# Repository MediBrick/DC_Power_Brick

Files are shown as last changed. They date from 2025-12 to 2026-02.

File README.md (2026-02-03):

# Power Brick

The Power Brick can control power to resistive heater, thermo electric cooler/heater or DC motor.
It requires 8V or larger input and might be able to handle 30A (4 oz copper).

## Two Channel DC Power Controller.
  - DRV8704 FET driver
  -  8..52V
  -  SPI interface for  monitoring
  -  PWM 500kHz
  -  CSD18540Q5B FET 30 / 400A (peak)

[Datasheet Driver](./datasheets/drv8704.pdf)
[Datasheet FET](./datasheets/csd18540q5b.pdf)

### Overview
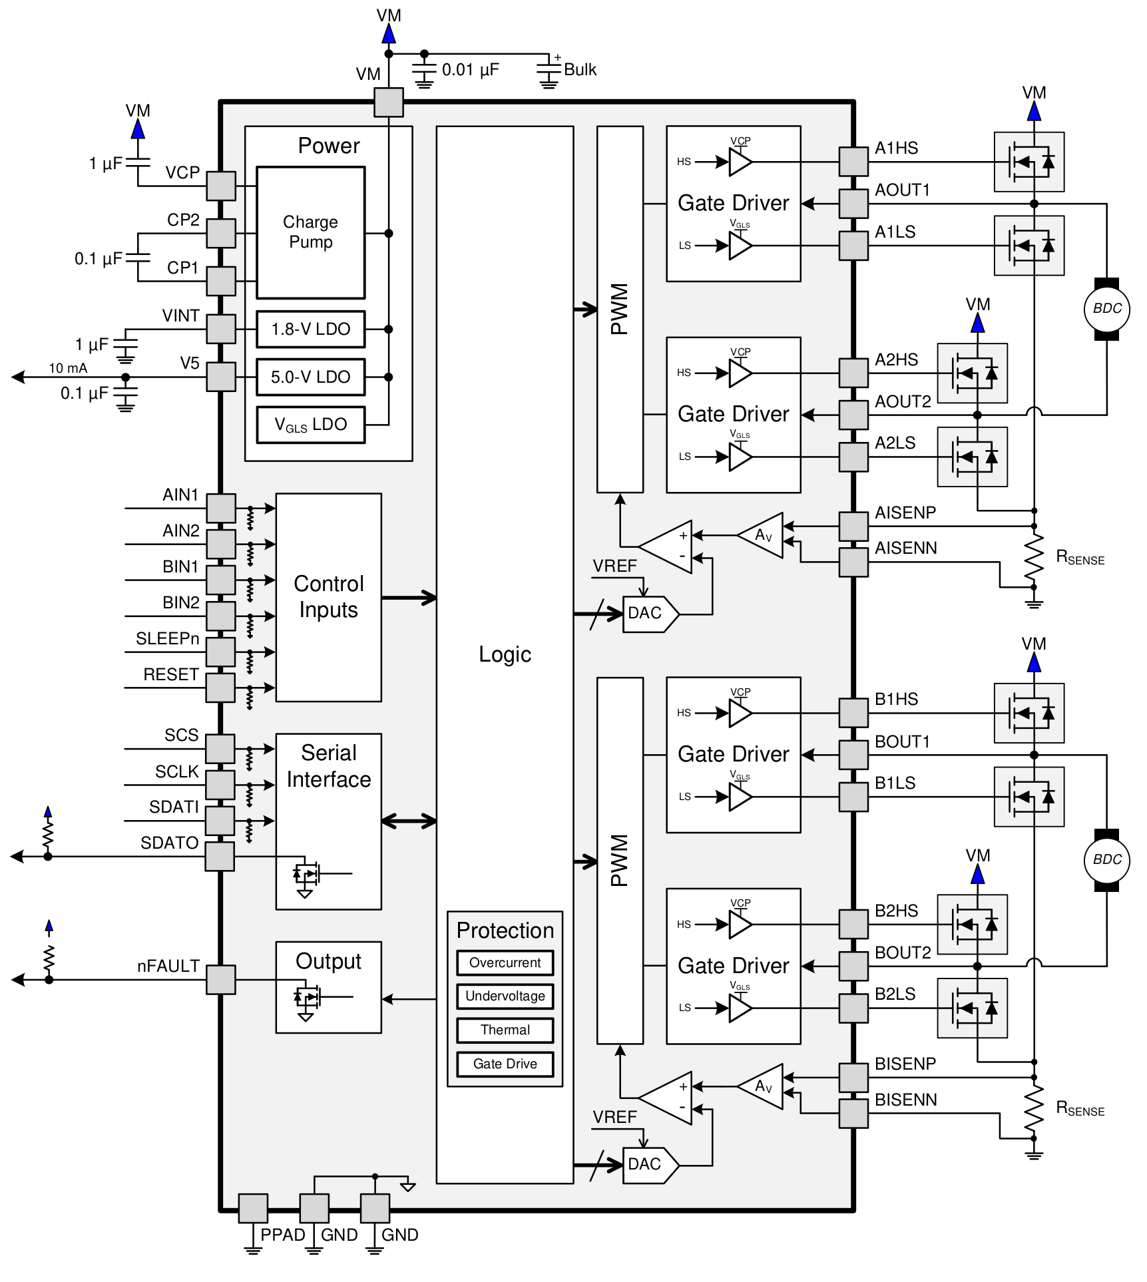
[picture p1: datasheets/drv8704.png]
DRV8704


### Control Logic
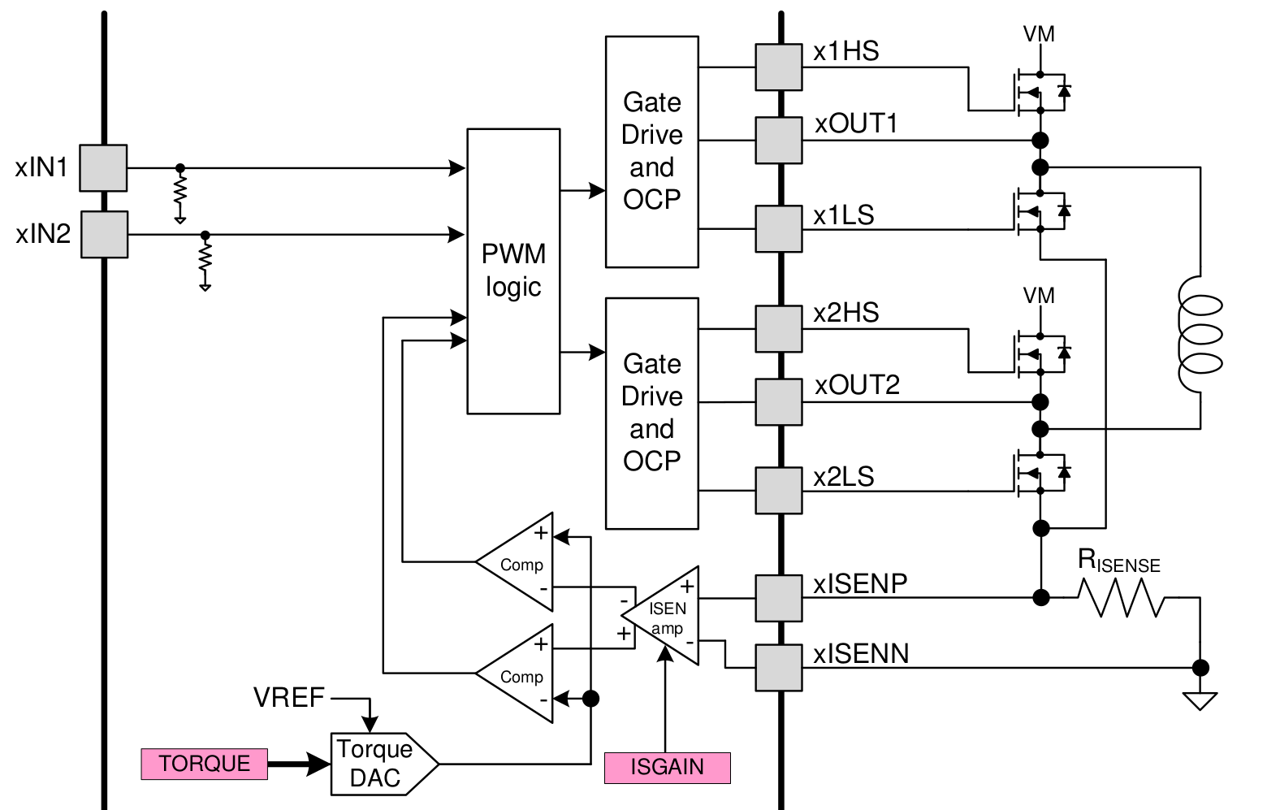
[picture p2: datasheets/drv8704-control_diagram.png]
DRV8704-diagram

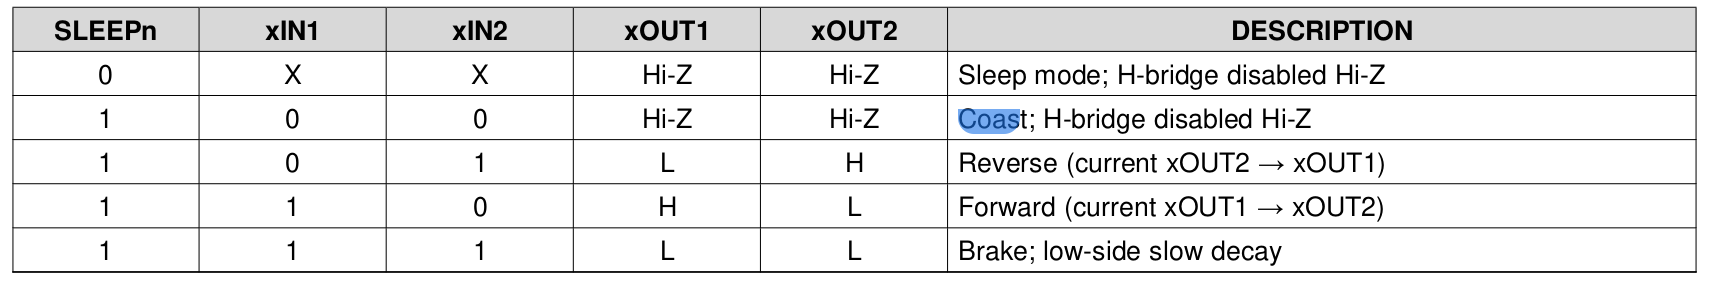
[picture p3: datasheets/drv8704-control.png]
DRV8704-control


## 2x Two Channel Precision Thermistor ADC
  - ADS1220
  - Configured for two channel 10K NTC thermistor measurements using internal current source and external reference 22k resistor.

[Datasheet ADS1220](./datasheets/ads1220.pdf)

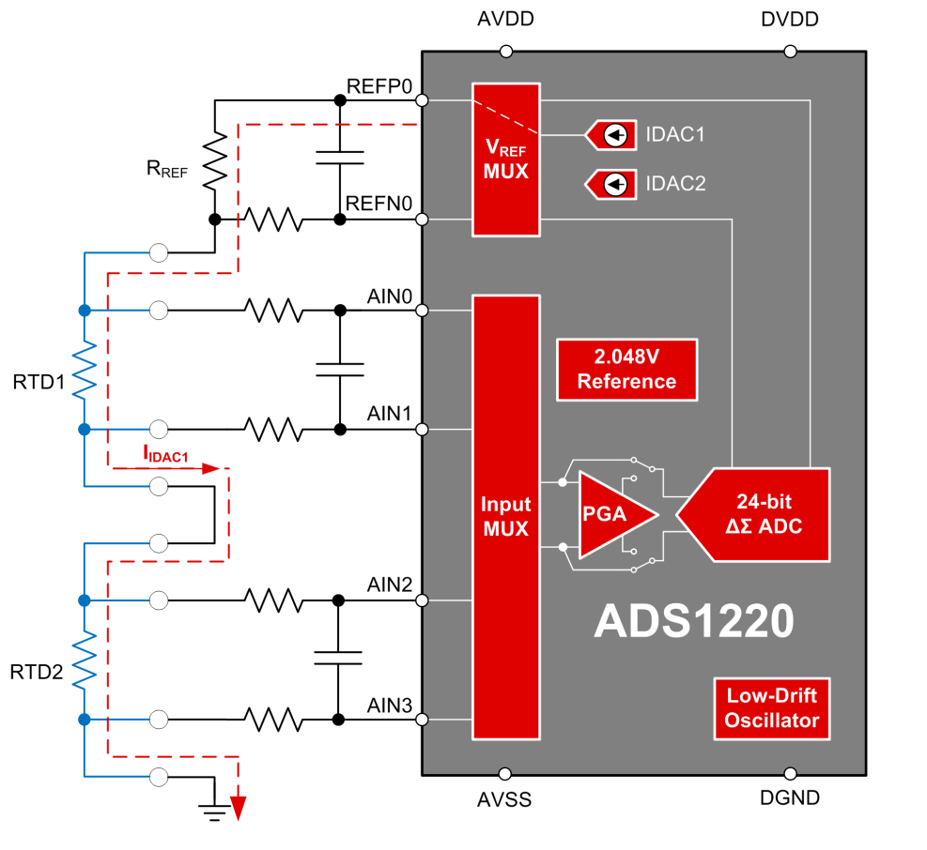
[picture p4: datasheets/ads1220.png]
ADS1220


This design requires that both temperature sensors are attached. If one is not populated, the measurement circuit is interrupted and no temperature is reported.

## Power Brick PCB Design

The following files were created for this project using KiCad.

Schematics

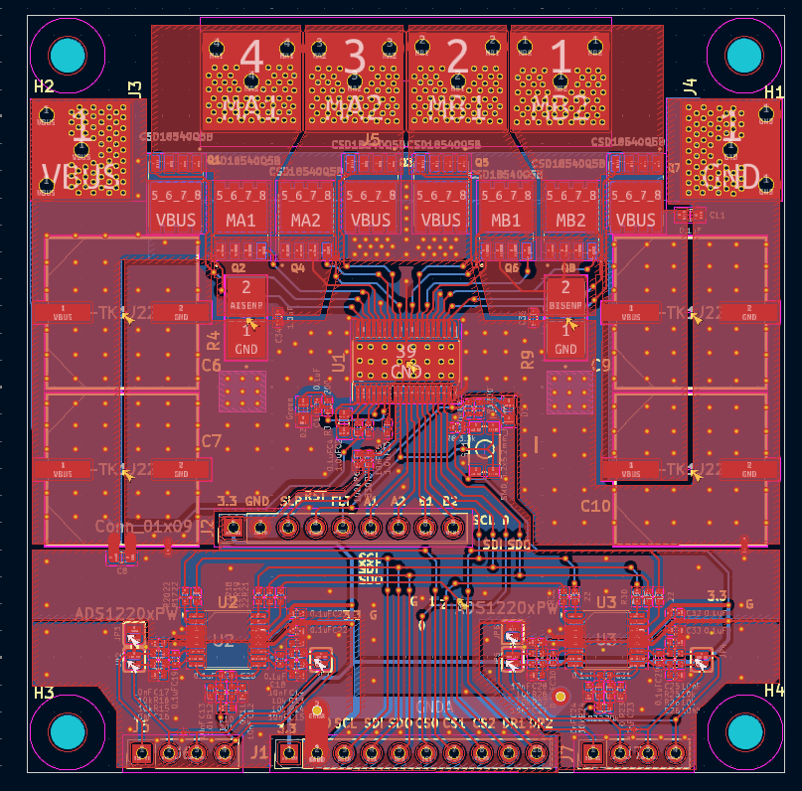
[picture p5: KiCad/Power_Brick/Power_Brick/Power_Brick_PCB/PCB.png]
Schematics

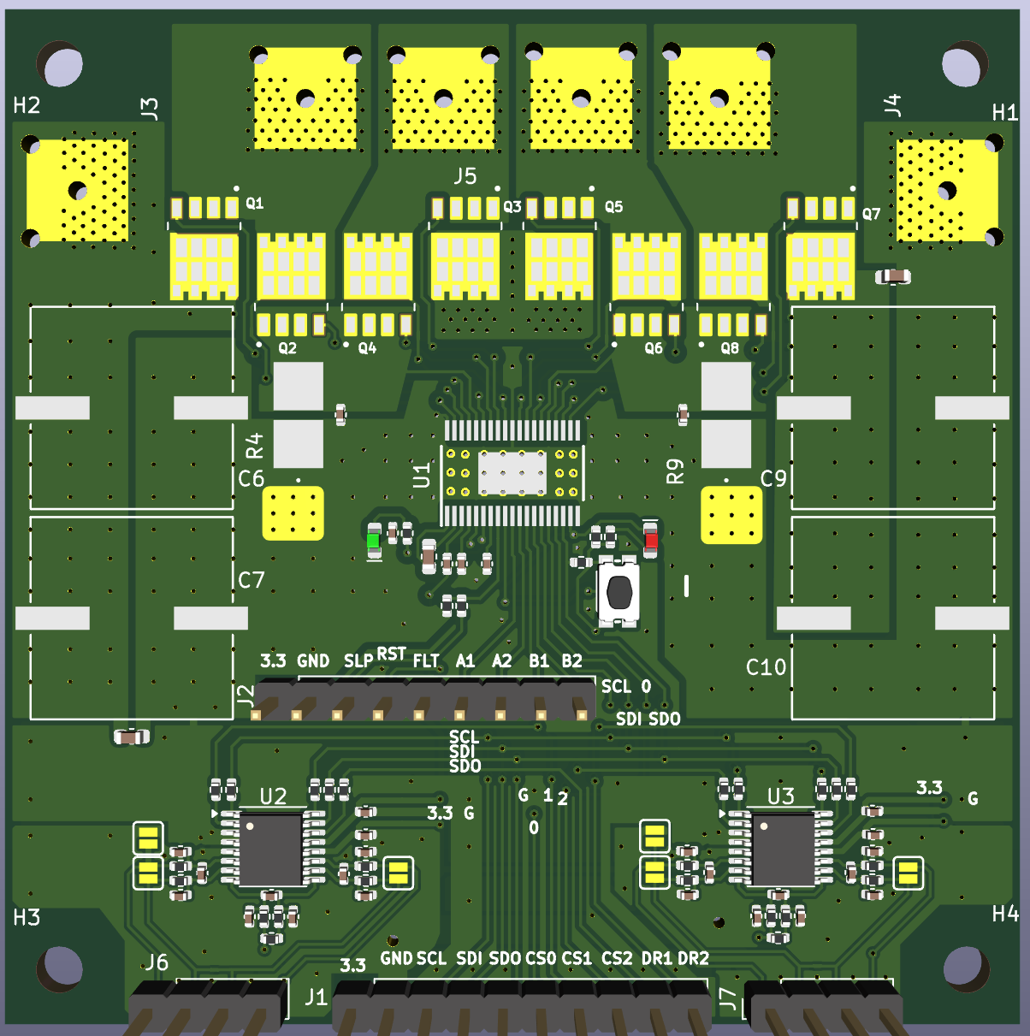
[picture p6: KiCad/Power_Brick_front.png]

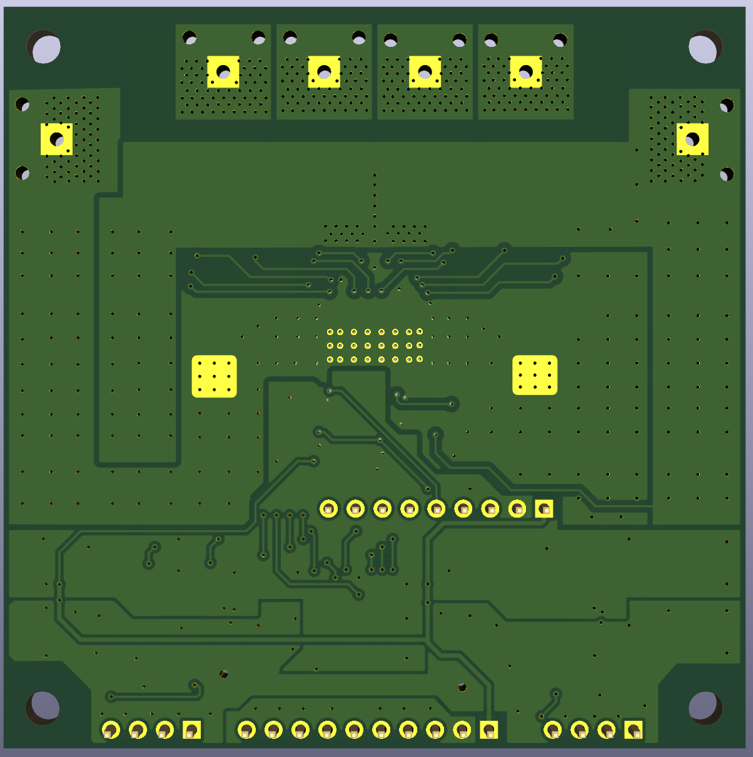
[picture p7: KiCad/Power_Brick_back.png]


[Bill of Materials](./DC%20Power%20Brick%20BOM.xlsx)
[Gerber Files](./)

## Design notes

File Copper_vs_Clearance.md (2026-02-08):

| Copper Weight (oz/ft²) | Thickness (µm) | Thickness (mm) | Standard Min Trace / Space (mm) | Advanced Min Trace / Space (mm) | Typical Use |
| --- | --- | --- | --- | --- | --- |
| 0.5 oz | ~18 µm | 0.018 mm | 0.10 / 0.10 | 0.075 / 0.075 | Fine-pitch logic |
| 1 oz | ~35 µm | 0.035 mm | 0.15 / 0.15 | 0.10 / 0.10 | General purpose  |
| 2 oz | ~70 µm | 0.070 mm | 0.20 / 0.20 | 0.15 / 0.15 | Moderate power |
| 3 oz | ~105 µm | 0.105 mm | 0.25 / 0.25 | 0.20 / 0.20 | Power drivers |
| 4 oz | ~140 µm | 0.140 mm | 0.30 / 0.30 | 0.25 / 0.25 | High current |
| 6 oz | ~210 µm | 0.210 mm | 0.40 / 0.40 | 0.30 / 0.30 | Power supplies |
| 8 oz | ~280 µm | 0.280 mm | 0.50 / 0.50 | 0.40 / 0.40 | Motor control |
| 10 oz | ~350 µm | 0.350 mm | 0.60 / 0.60 | 0.50 / 0.50 | Industrial power |
| 12 oz | ~420 µm | 0.420 mm | 0.75 / 0.75 | 0.60 / 0.60 | Extreme current  |

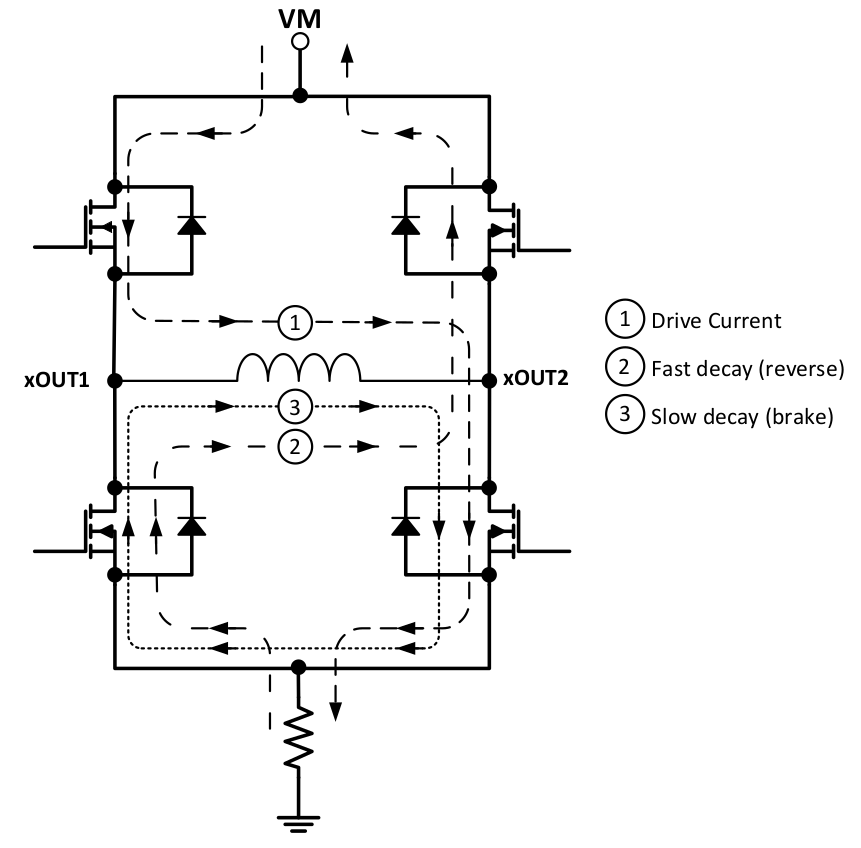
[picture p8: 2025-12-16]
datasheets/H-Bridge.png

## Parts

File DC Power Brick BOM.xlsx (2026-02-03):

Item # | Designator | Qty | Manufacturer | Mfg Part # | LCSC Part# | U.S. Distributor | Description / Value | Packaging | Type | Cost | Footprint | Remark
1 | C17,C26,C15,C5,C13,C24,C16,C12,C14,C28,C27,C23,C25 | 13 | Samsung Electro-Mechanics (https://www.lcsc.com/brand-detail/254.html) | CL05B103KC5VPNC | C16193410 (https://www.lcsc.com/product-detail/C16193410.html) |  | 10nF X7R ±10% 100V 0402 Ceramic Capacitors RoHS | 402 | SMD |  | C_0402_1005Metric
2 | Q2,Q8,Q6,Q5,Q4,Q3,Q7,Q1 | 8 | TI | CSD18540Q5B | C86513 (https://www.lcsc.com/product-detail/C86513.html?s_z=n_CSD18540Q5B) |  | CSD18540Q5B MOSFET N CH 60V |  | SMD | 1.5 | TRANS_CSD18540Q5B
3 | R25,R14,R28,R13,R2,R16,R26,R12,R24,R15,R27 | 11 | YAGEO (https://www.lcsc.com/brand-detail/396.html) | RC0402FR-0710KL | C60490 (https://www.lcsc.com/product-detail/C60490.html?s_z=n_402%252010K) |  | RES 10kΩ ±1% 62.5mW 0402 | 402 | SMD |  | R_0402_1005Metric
4 | C10,C7,C6,C9 | 4 | PANASONIC (https://www.lcsc.com/brand-detail/121.html) | EEETK1J221AQ | C401915 (https://www.lcsc.com/product-detail/C401915.html?s_z=n_EEE-TK1J221AQ) | Digikey Link incase LCSC is outofstock (https://www.digikey.com/en/products/detail/panasonic-electronic-components/EEE-TK1J221AQ/1975563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) | CAP ALUM 220uF ±20% 63V SMD |  | SMD | 3 | CAP_PAN_EEE_H13_PAN
5 | R32,R19,R29,R21,R31,R33,R30,R20,R18,R17 | 10 | YAGEO (https://www.lcsc.com/brand-detail/396.html) | RC0402FR-0722RL | C114765 (https://www.lcsc.com/product-detail/C114765.html?s_z=n_402%252022) |  | RES 22Ω ±1% 62.5mW 0402 | 402 | SMD |  | R_0402_1005Metric
6 | R10,R22 | 2 | YAGEO (https://www.lcsc.com/brand-detail/396.html) | RC0402FR-0720KL | C93942 (https://www.lcsc.com/product-detail/C93942.html?s_z=n_402%252020k) |  | RES 20kΩ ±1% 62.5mW 0402 | 402 | SMD |  | R_0402_1005Metric
7 | C4,C8,C11 | 3 | Samsung Electro-Mechanics (https://www.lcsc.com/brand-detail/254.html) | CL10B104KC8NNNC | C15725 (https://www.lcsc.com/product-detail/C15725.html) |  | CAP CER 100nF 100V X7R 0603 | 603 | SMD |  | C_0603_1608Metric
8 | C34,C35 | 2 | Samsung Electro-Mechanics (https://www.lcsc.com/brand-detail/254.html) | CL05B102KC5VPNC | C2976448 (https://www.lcsc.com/product-detail/C2976448.html) |  | CAP CER 1nF 100V X7R 0402 | 402 | SMD |  | C_0402_1005Metric
9 | R3,R1 | 2 | YAGEO (https://www.lcsc.com/brand-detail/396.html) | RC0402FR-07200RL | C114764 (https://www.lcsc.com/product-detail/C114764.html?s_z=n_402%2520200) |  | RES 200Ω ±1% 62.5mW 0402 | 402 | SMD |  | R_0402_1005Metric
10 | C3,C2 | 2 | Samsung Electro-Mechanics (https://www.lcsc.com/brand-detail/254.html) | CL05A105KO5NNNC | C29266 (https://www.lcsc.com/product-detail/C29266.html) |  | CAP CER 1uF 16V X5R 0402 | 402 | SMD |  | C_0402_1005Metric
11 | C30,C31,C20,C33,C22,C32,C21,C29,C19,C18,C1 | 11 | Samsung Electro-Mechanics (https://www.lcsc.com/brand-detail/254.html) | CL05B104KO5NNNC | C1525 (https://www.lcsc.com/product-detail/C1525.html?s_z=n_CAP%2520CER%2520100nF%252016V%2520X7R%25200402) |  | CAP CER 100nF 16V X7R 0402 | 402 | SMD |  | C_0402_1005Metric
12 | R23,R11 | 2 | YAGEO (https://www.lcsc.com/brand-detail/396.html) | RC0402FR-070RL | C106231 (https://www.lcsc.com/product-detail/C106231.html?s_z=n_RC0402FR-070RL) |  | RES 0Ω ±1% 62.5mW 0402 | 402 | SMD |  | R_0402_1005Metric
13 | R4,R9 | 2 | YAGEO (https://www.lcsc.com/brand-detail/396.html) | PA2512FKE7T0U5E | C6730280 (https://www.lcsc.com/product-detail/C6730280.html?s_z=n_PA2512FKE7T0U5E) |  | RES 0.5mΩ ±1% 3W 2512, Current Sense | 2512 | SMD |  | RES_PA2512_YAG
14 | R7 | 1 | YAGEO (https://www.lcsc.com/brand-detail/396.html) | RC0402FR-07330RL | C105875 (https://www.lcsc.com/product-detail/C105875.html?s_z=n_RC0402FR-07330RL) |  | RES 330Ω ±1% 62.5mW 0402 | 402 | SMD |  | R_0402_1005Metric
15 | R6 | 1 | YAGEO (https://www.lcsc.com/brand-detail/396.html) | RC0402FR-07100KL | C60491 (https://www.lcsc.com/product-detail/C60491.html?s_z=n_RC0402FR-07100kL) |  | RES 100kΩ ±1% 62.5mW 0402 | 402 | SMD |  | R_0402_1005Metric
16 | R8 | 1 | YAGEO (https://www.lcsc.com/brand-detail/396.html) | RC0402FR-073K3L | C137992 (https://www.lcsc.com/product-detail/C137992.html?s_z=n_RC0402FR%25203.3k) |  | RES 3.3kΩ ±1% 62.5mW 0402 | 402 | SMD |  | R_0402_1005Metric
17 | U1 | 1 | TI | DRV8704DCPR | C701787 (https://www.lcsc.com/product-detail/C701787.html?s_z=n_DRV8704DCPR) |  | HTSSOP-38-EP-4.4mm Motor Drivers, Controllers RoHS | HTSSOP-38-EP-4.4mm | SMD | 6 | DCP0038A_N
18 | U2,U3 | 2 | TI | ADS1220IPW (https://www.ti.com/product/ADS1220/part-details/ADS1220IPW) | C1542855 (https://www.lcsc.com/product-detail/C1542855.html?s_z=n_ADS1220xPW) | Digikey Link incase LCSC is outofstock (https://www.digikey.com/en/products/detail/texas-instruments/ADS1220IPW/4311719) | -40℃~+125℃ SPI 2.3V~5.5V 2kHz TSSOP-16 Analog to Digital Converters (ADC) RoHS | TSSOP-16 | SMD | $11.0000 | TSSOP-16_4.4x5mm_P0.65mm
19 | D1 | 1 | XINGLIGHT (https://www.lcsc.com/brand-detail/12469.html) | XL-1608SURC-06 | C965799 (https://www.lcsc.com/product-detail/C965799.html?s_z=n_LED_0603_1608Metric_Red) |  | Red LED | 603 | SMD |  | LED_0603_1608Metric_Red
20 | D2 | 1 | XINGLIGHT (https://www.lcsc.com/brand-detail/12469.html) | XL-1608UGC-06A | C7371903 (https://www.lcsc.com/product-detail/C7371903.html?s_z=n_XL-1608UGC-06) |  | Green LED | 603 | SMD |  | LED_0603_1608Metric_Green
21 | SW1 | 1 | C&K (https://www.lcsc.com/brand-detail/11534.html) | KMR211NGLFS | C221676 (https://www.lcsc.com/product-detail/C221676.html?s_z=n_KMR2) |  | SWITCH TACTILE SPST-NO 120gf SMD |  | SMD |  | Push_SMD_4.6x2.8mm_h1.9mm
22 | JP1,JP2,JP4,JP5,JP3,JP6 | 6 |  |  |  |  | Jumper_2_Bridged |  |  |  | Jumper_2_NO | DO NOT POPULATE
23 | J1 | 1 |  |  |  |  | Conn_01x10 |  | SMD |  | PinHeader_1x10_P2.54mm_Vertical | DO NOT POPULATE
24 | J6,J7 | 2 |  |  |  |  | Conn_01x04 |  | SMD |  | PinHeader_1x04_P2.54mm_Vertical | DO NOT POPULATE
25 | J4,J3 | 2 |  |  |  |  | MKDS5_2-9_5_1pos_PowerPad |  | SMD |  | MKDS5_2-9_5_1pos_PowerPad | DO NOT POPULATE
26 | J2 | 1 |  |  |  |  | Conn_01x09 |  | SMD |  | PinHeader_1x09_P2.54mm_Vertical | DO NOT POPULATE
27 | J5 | 1 |  |  |  |  | MKDS5_2-9_5_4pos_PowerPad |  | SMD |  | MKDS5_2-9_5_4pos_PowerPad | DO NOT POPULATE

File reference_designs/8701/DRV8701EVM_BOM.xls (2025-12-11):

DRV8701EVM
Designator | Quantity | Value | Description | PackageReference | PartNumber | Manufacturer | Alternate PartNumber | Alternate Manufacturer
!PCB1 | 1 |  | Printed Circuit Board |  | DRV8701EVM | Any
C1, C2 | 2 | 470uF | CAP, AL, 470 µF, 50 V, +/- 20%, ohm, TH | D10xL20mm | ECA-1HM471 | Panasonic
C3, C20 | 2 | 4.7uF | CAP, CERM, 4.7uF, 10V, +/-20%, X7R, 0805 | 0805 | C2012X7R1A475M | TDK
C4, C18, C21 | 3 | 0.1uF | CAP, CERM, 0.1uF, 10V, +/-10%, X7R, 0603 | 0603 | C0603C104K8RACTU | Kemet
C5, C6 | 2 | 1uF | CAP, CERM, 1uF, 50V, +/-10%, X7R, 0805 | 0805 | GRM21BR71H105KA12L | MuRata
C7, C8, C13, C14 | 4 | DNP | CAP, CERM, 0.01uF, 50V, +/-10%, X7R, 0603 | 0603 | DNP | DNP
C9 | 1 | 1uF | CAP, CERM, 1uF, 16V, +/-10%, X7R, 0603 | 0603 | C1608X7R1C105K | TDK
C10 | 1 | 10uF | CAP, CERM, 10uF, 50V, +/-10%, X7R, 1210 | 1210 | GRM32ER71H106KA12L | MuRata
C11, C12 | 2 | 0.1uF | CAP, CERM, 0.1uF, 50V, +/-10%, X7R, 0603 | 0603 | C1608X7R1H104K | TDK
C15, C16, C19 | 3 | 1uF | CAP, CERM, 1uF, 6.3V, +/-10%, X7R, 0603 | 0603 | GRM188R70J105KA01D | MuRata
C17 | 1 | 1000pF | CAP, CERM, 1000pF, 16V, +/-10%, X7R, 0402 | 0402 | GRM155R71C102KA01D | MuRata
C22 | 1 | 1000pF | CAP, CERM, 1000pF, 16V, +/-10%, X7R, 0603 | 0603 | GRM188R71C102KA01D | MuRata
D1, D4 | 2 | Green | LED, Green, SMD | LED_0805 | LTST-C171GKT | Lite-On | 150080VS75000 | Wurth Elektronik
D2, D3 | 2 | Red | LED, Red, SMD | LED_0805 | LTST-C170KRKT | Lite-On | 150080SS75000 | Wurth Elektronik
F1 | 1 | 1206L050/15YR | Fuse, Poly Resetable PTC, 0.5A | 1206 | 1206L050/15YR | Littelfuse
FID1, FID2, FID3 | 3 |  | Fiducial mark. There is nothing to buy or mount. | Fiducial | N/A | N/A
H1, H2, H3, H4 | 4 |  | Machine Screw, Round, #4-40 x 1/4, Nylon, Philips panhead | Screw | NY PMS 440 0025 PH | B&F Fastener Supply
H5, H6, H7, H8 | 4 |  | Standoff, Hex, 0.5"L #4-40 Nylon | Standoff | 1902C | Keystone
H9 | 1 |  | Connector, micro USB Type B, Receptacle, R/A, SMD | Micro USB-B | ZX62-B-5PA(11) | Hirose Electric Co. Ltd.
H10, H11 | 2 |  | Terminal Block, 5 mm, 2x1, Tin, TH | Terminal Block, 5 mm, 2x1, TH | 691 101 710 002 | Wurth Elektronik eiSos
H12 | 1 |  | Header, 100mil, 10x1, Gold, TH | 10x1 Header | TSW-110-07-G-S | Samtec | 61301011121 | Wurth Elektronik
J1 | 1 |  | Header, 100mil, 6x2, Tin, TH | Header, 6x2, 100mil, Tin | PEC06DAAN | Sullins Connector Solutions | 61300621121 | Wurth Elektronik
J2 | 1 |  | Header, 100mil, 3x1, Tin, TH | Header, 3 PIN, 100mil, Tin | PEC03SAAN | Sullins Connector Solutions | 61300311121 | Wurth Elektronik
J3 | 1 |  | SOCKET .050" GRID SIP 4 POS R/A, TH | R/A 4x1 receptacle | 851-43-004-20-001000 | Mill-Max
Q1, Q2, Q3, Q4 | 4 | 60V | MOSFET, N-CH, 60V, 172A, SON 5x6mm | SON 5x6mm | CSD18532Q5B | Texas Instruments
R1, R2, R3, R4, R10, R12, R14, R16, R18, R20, R21, R22, R29 | 13 | 0 | RES, 0 ohm, 5%, 0.1W, 0603 | 0603 | CRCW06030000Z0EA | Vishay-Dale
R5, R7, R11 | 3 | 10k | RES, 10k ohm, 5%, 0.1W, 0603 | 0603 | CRCW060310K0JNEA | Vishay-Dale
R6, R8 | 2 | DNP | RES, 0 ohm, 5%, 0.1W, 0603 | 0603 | DNP | DNP
R9 | 1 | 0.01 | RES, 0.01 ohm, 1%, 3W, 2512 | 2512 | CRA2512-FZ-R010ELF | Bourns
R13 | 1 | 68k | RES, 68k ohm, 5%, 0.1W, 0603 | 0603 | CRCW060368K0JNEA | Vishay-Dale
R15, R17 | 2 | 47k | RES, 47k ohm, 5%, 0.1W, 0603 | 0603 | CRCW060347K0JNEA | Vishay-Dale
R19 | 1 | 50k | Trimming Potentiometer, 50K, 0.5W, TH | 9.53x8.89mm | 3352T-1-503LF | Bourns
R23, R24, R25 | 3 | 330 | RES, 330 ohm, 5%, 0.1W, 0603 | 0603 | CRCW0603330RJNEA | Vishay-Dale
R26 | 1 | 4.99k | RES, 4.99k ohm, 1%, 0.1W, 0603 | 0603 | CRCW06034K99FKEA | Vishay-Dale
R27 | 1 | 200k | RES, 200k ohm, 5%, 0.1W, 0603 | 0603 | CRCW0603200KJNEA | Vishay-Dale
R28 | 1 | 33k | RES, 33k ohm, 5%, 0.1W, 0603 | 0603 | CRCW060333K0JNEA | Vishay-Dale
R30 | 1 | 7.5k | RES, 7.5 k, 5%, 0.1 W, 0603 | 0603 | CRCW06037K50JNEA | Vishay-Dale
R31 | 1 | 10k | RES, 10 k, 5%, 0.1 W, 0603 | 0603 | CRCW060310K0JNEA | Vishay-Dale
S1 | 1 |  | Switch, Tactile, SPST-NO, 0.05A, 12V, SMT | SW, SPST 6x6 mm | 4-1437565-1 | TE Connectivity
SH-J1, SH-J2 | 2 | 1x2 | Shunt, 100mil, Gold plated, Black | Shunt | 969102-0000-DA | 3M | SNT-100-BK-G | Samtec
TP1, TP2, TP3 | 3 | Red | Test Point, Compact, Red, TH | Red Compact Testpoint | 5005 | Keystone
TP4, TP12, TP19 | 3 | Black | Test Point, Compact, Black, TH | Black Compact Testpoint | 5006 | Keystone
TP5, TP6, TP7, TP8, TP9, TP10 | 6 | White | Test Point, Compact, White, TH | White Compact Testpoint | 5007 | Keystone
TP14 | 1 |  | 1mm Uninsulated Shorting Plug, 10.16mm spacing, TH | Shorting Plug, 10.16mm spacing, TH | D3082-05 | Harwin
U1 | 1 |  | H-Bridge Gate Driver, RGE0024F | RGE0024F | DRV8701ERGER | Texas Instruments | DRV8701ERGET | Texas Instruments
U2 | 1 |  | USB to Serial UART, SSOP28 | SSOP28 | FT232RL | FTDI
U3 | 1 |  | 16 MHz Mixed Signal Microcontroller with 16 KB Flash, 512 B SRAM and 24 GPIOs, -40 to 85 degC, 20-pin SOP (PW), Green (RoHS & no Sb/Br) | PW0020A | MSP430G2553IPW20 | Texas Instruments
 |  | Notes:
 |  | Unless otherwise noted in the Alternate PartNumber and/or Alternate Manufacturer columns, all parts may be substituted with equivalents.

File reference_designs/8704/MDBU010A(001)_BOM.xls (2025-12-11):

Filename: | MDBU010A(001)_BOM.xls
Variant: | 001
Generated: | 10/7/2015 4:07:28 PM
 |  | DRV8704 EVM
Designator | Quantity | Value | Description | PackageReference | PartNumber | Manufacturer | Alternate PartNumber | Alternate Manufacturer
!PCB | 1 |  | Printed Circuit Board |  | MDBU010 | Any | - | -
C1, C4 | 2 | 0.1uF | CAP, CERM, 0.1 µF, 16 V, +/- 20%, X7R, 0603 | 0603 | C0603C104M4RACTU | Kemet
C2, C5 | 2 | 0.01uF | CAP, CERM, 0.01 µF, 25 V, +/- 10%, X7R, 0402 | 0402 | GCM155R71E103KA37D | MuRata
C3, C6 | 2 | 0.01uF | CAP, CERM, 0.01 µF, 50 V, +/- 10%, X7R, 0603 | 0603 | C0603X103K5RACTU | Kemet
C7 | 1 | 1uF | CAP, CERM, 1 µF, 16 V, +/- 10%, X7R, 0603 | 0603 | EMK107B7105KA-T | Taiyo Yuden
C8 | 1 | 0.1uF | CAP, CERM, 0.1 µF, 50 V, +/- 10%, X7R, 0805 | 0805 | GRM21BR71H104KA01L | MuRata
C9 | 1 | 1uF | CAP, CERM, 1 µF, 16 V, +/- 10%, X5R, 0402 | 0402 | EMK105BJ105KVHF | Taiyo Yuden
C10 | 1 | 0.01uF | CAP, CERM, 0.01 µF, 50 V, +/- 5%, X7R, 0402 | 0402 | C0402C103J5RACTU | Kemet
C11 | 1 | 0.1uF | CAP, CERM, 0.1 µF, 10 V, +/- 10%, X5R, 0402 | 0402 | GRM155R61A104KA01D | MuRata
C12, C14, C16, C17 | 4 | 220uF | CAP, AL, 220 µF, 63 V, +/- 20%, 0.26 ohm, AEC-Q200 Grade 1, SMD | SMT Radial H13 | EEE-TK1J221AQ | Panasonic
C13, C15 | 2 | 0.1uF | CAP, CERM, 0.1 µF, 50 V, +/- 10%, X7R, 0402 | 0402 | C1005X7R1H104K050BB | TDK
D1, D2, D3, D4 | 4 | 40V | Diode, Schottky, 40 V, 1 A, MicroSMP | MicroSMP | MSS1P4-M3/89A | Vishay-Siliconix
D5 | 1 | 5.1V | Diode, Zener, 5.1 V, 250 mW, SOD-323 | SOD-323 | CMDZ5L1 TR | Central Semiconductor
D6 | 1 | Red | LED, Red, SMD | LED_0805 | 150080SS75000 | Wurth Elektronik
D7 | 1 | Green | LED, Green, SMD | LED_0603 | 150060VS75000 | Wurth Elektronik
J1, J3, J5, J7 | 4 |  | Header, 1x1, Tin, TH | Header, 1x1 | PEC01SAAN | Sullins Connector Solutions
J2, J4, J6, J8 | 4 |  | Header, 100mil, 3x1, Tin, TH | Header, 3 PIN, 100mil, Tin | PEC03SAAN | Sullins Connector Solutions
J9, J10, J11 | 3 |  | Terminal Block, 5 mm, 2x1, Tin, TH | Terminal Block, 5 mm, 2x1, TH | 691 101 710 002 | Wurth Elektronik
J12, J13 | 2 |  | Connector, Receptacle, 100mil, 10x1, Gold plated, TH | 10x1 Receptacle | SSW-110-23-F-S | Samtec
J14 | 1 |  | 1mm Uninsulated Shorting Plug, 10.16mm spacing, TH | Shorting Plug, 10.16mm spacing, TH | D3082-05 | Harwin
Q1, Q2, Q3, Q4, Q5, Q6, Q7, Q8 | 8 | 60V | MOSFET, N-CH, 60 V, 28 A, SON 5x6mm | SON 5x6mm | CSD18540Q5B | Texas Instruments |  | None
R1, R3 | 2 | 5k | TRIMMER, 5k ohm, 0.5W, TH | 375x190x375mil | 3386P-1-502LF | Bourns
R1Sense, R2Sense, R3Sense, R4Sense | 4 | 0.015 | RES, 0.015, 1%, 2 W, 2512 | 2512 | CSRN2512FK15L0 | Stackpole Electronics Inc
R2, R4 | 2 | 10.0k | RES, 10.0 k, 1%, 0.1 W, 0603 | 0603 | ERJ-3EKF1002V | Panasonic
R5, R16 | 2 | 200 | RES, 200, 1%, 0.063 W, 0402 | 0402 | CRCW0402200RFKED | Vishay-Dale
R6, R7 | 2 | 100k | RES, 100 k, 5%, 0.063 W, 0402 | 0402 | CRCW0402100KJNED | Vishay-Dale
R8, R9, R10, R11, R12, R13, R14, R15 | 8 | 0 | RES, 0, 5%, 0.063 W, 0402 | 0402 | CRCW04020000Z0ED | Vishay-Dale
R23 | 1 | 10k | RES, 10 k, 5%, 0.063 W, 0402 | 0402 | CRCW040210K0JNED | Vishay-Dale
S1 | 1 |  | Switch, Tactile, SPST-NO, 0.05A, 12V, SMT | SW, SPST 6x6 mm | 4-1437565-1 | TE Connectivity
TP1, TP2, TP3, TP4, TP5 | 5 | SMT | Test Point, Compact, SMT | Testpoint_Keystone_Compact | 5016 | Keystone
U1, U2 | 2 |  | LinCMOS Timer, D0008A | D0008A | TLC555CD | Texas Instruments |  | Texas Instruments
U3 | 1 |  | 52-V Dual H-Bridge PWM Gate Driver, DCP0038A | DCP0038A | DRV8704DCPR | Texas Instruments | DRV8704DCP | Texas Instruments
C18, C19 | 0 | 1000pF | CAP, CERM, 1000 pF, 25 V, +/- 5%, C0G/NP0, 0402 | 0402 | C1005C0G1E102J | TDK
FID1, FID2, FID3 | 0 |  | Fiducial mark. There is nothing to buy or mount. | Fiducial | N/A | N/A
R17, R18, R19, R20, R21, R22, R26 | 0 | 0 | RES, 0, 5%, 0.063 W, 0402 | 0402 | CRCW04020000Z0ED | Vishay-Dale
R24 | 0 | 3.3k | RES, 3.3 k, 5%, 0.063 W, 0402 | 0402 | CRCW04023K30JNED | Vishay-Dale
 |  | Notes:
 |  | Unless otherwise noted in the Alternate PartNumber and/or Alternate Manufacturer columns, all parts may be substituted with equivalents.

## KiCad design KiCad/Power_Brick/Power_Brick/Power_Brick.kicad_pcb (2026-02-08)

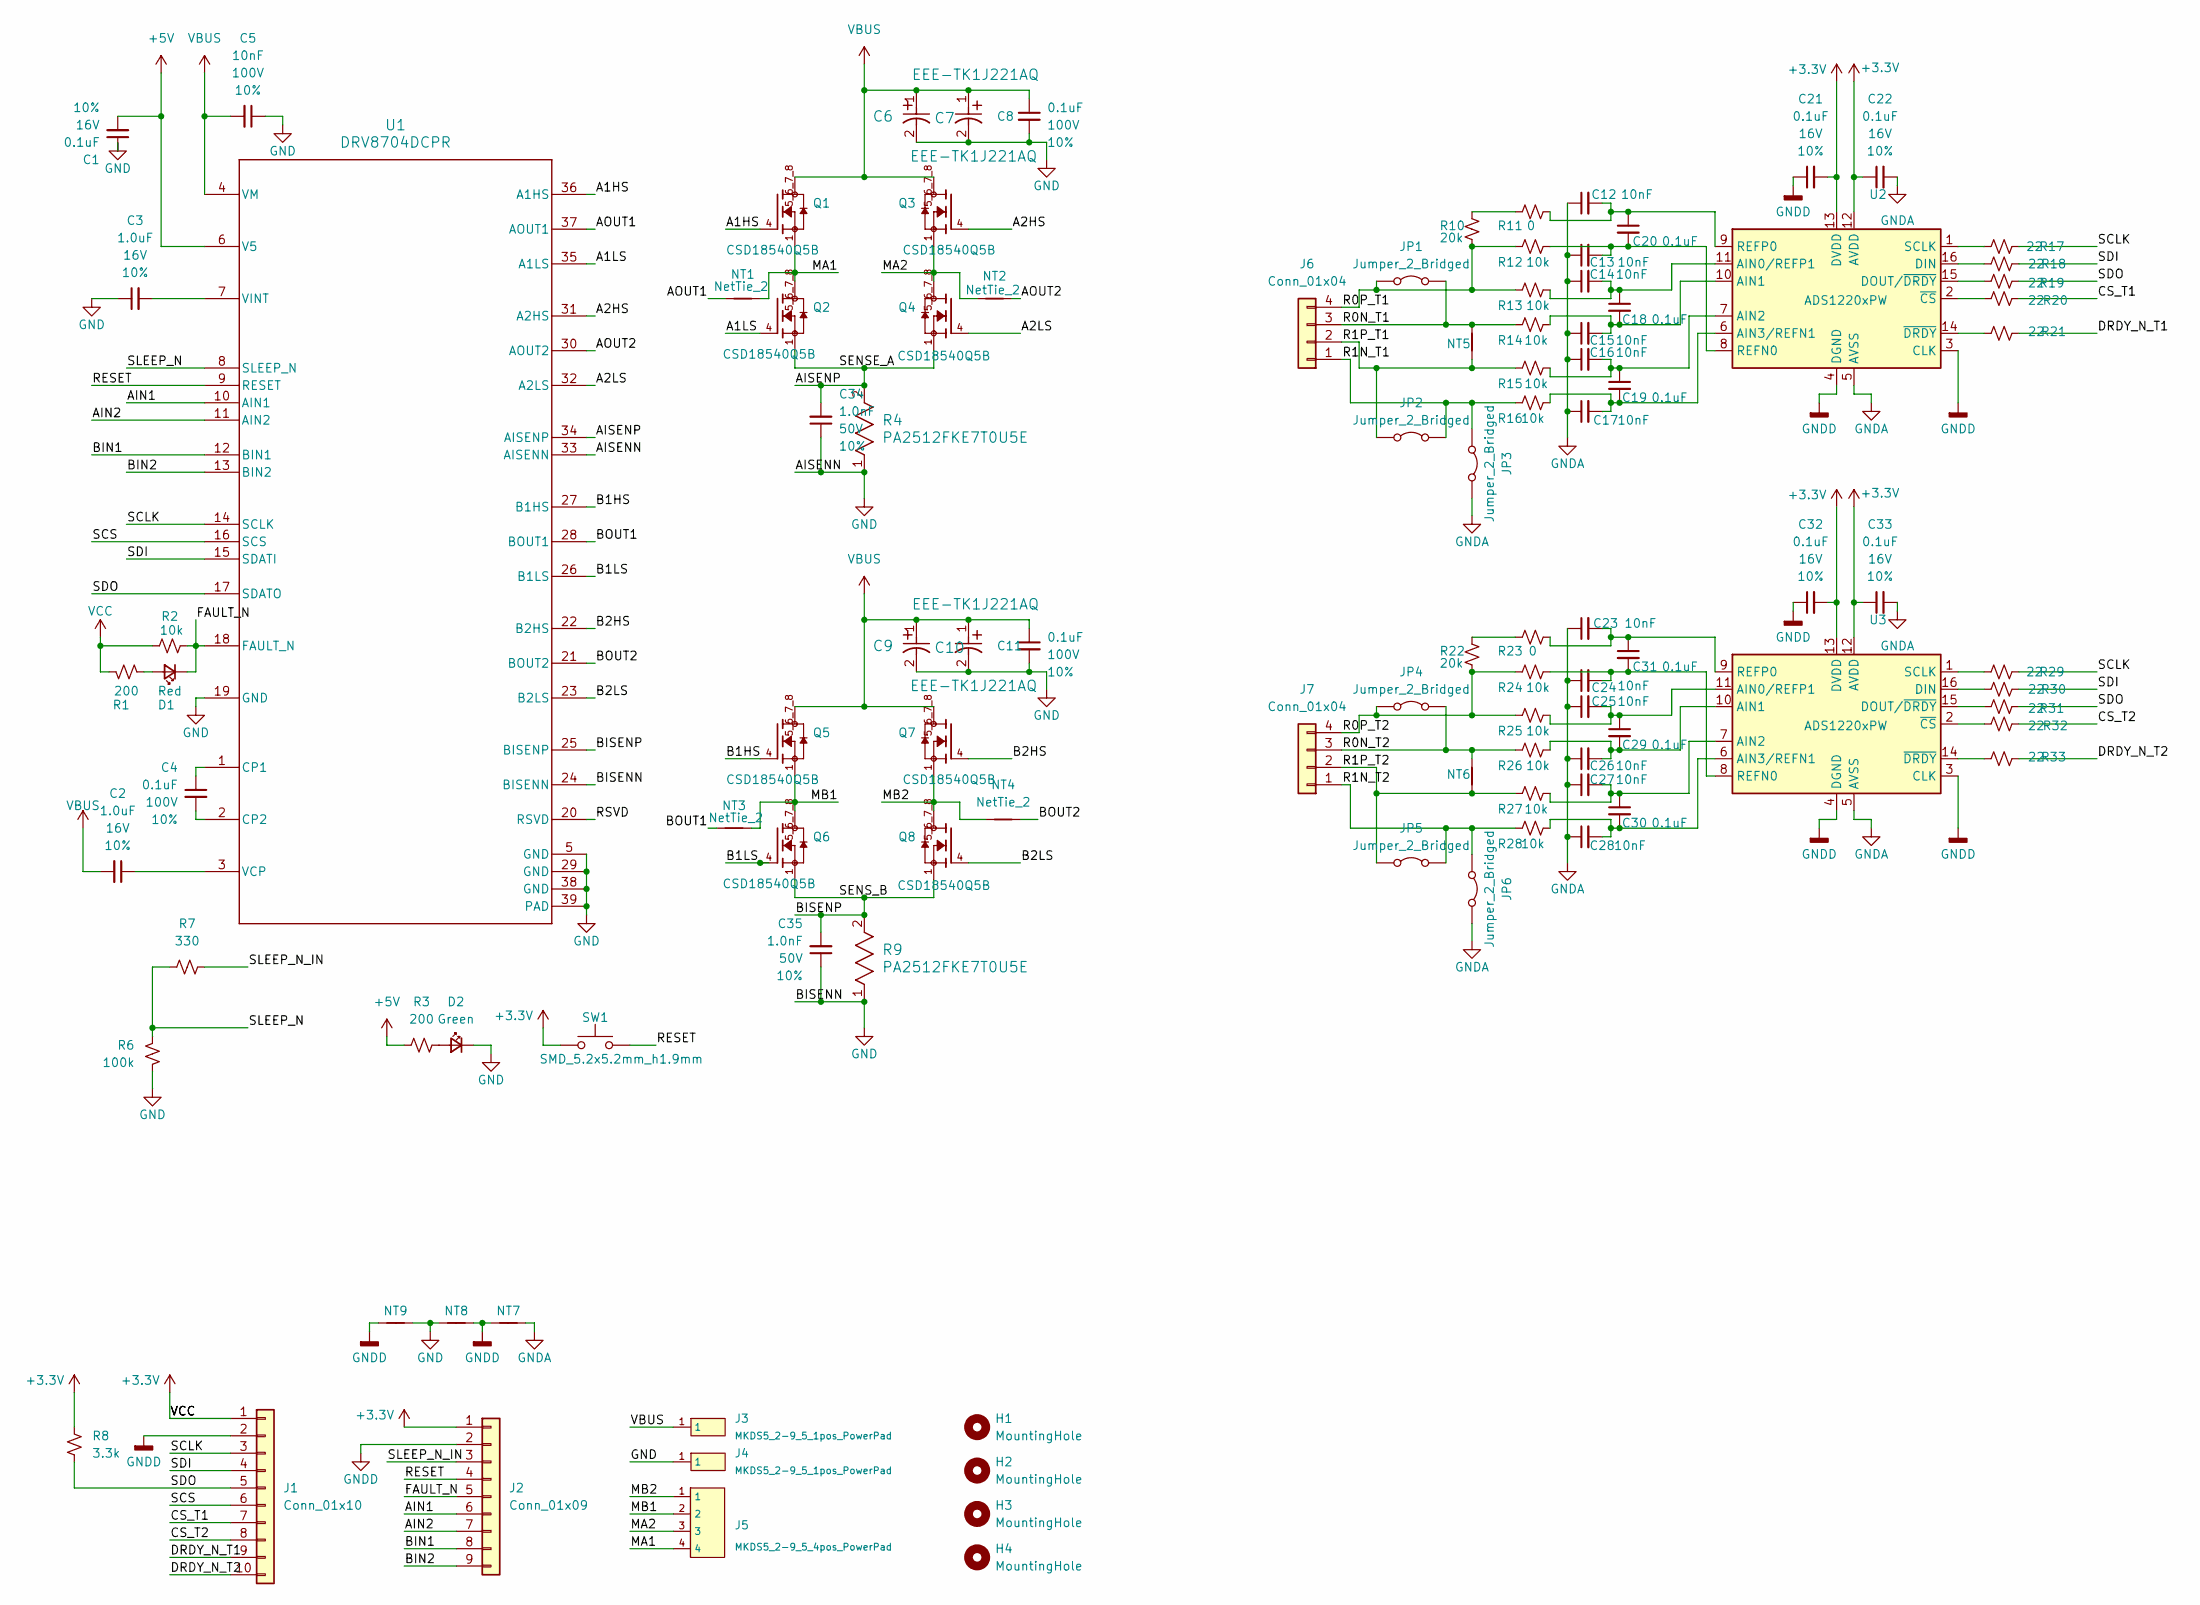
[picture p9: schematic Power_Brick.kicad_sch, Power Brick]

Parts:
C1, C18, C19, C20, C21, C22, C29, C30, C31, C32, C33: 0.1uF; C_0402_1005Metric; Voltage 16V; Tolerance 10%
C2, C3: 1.0uF; C_0402_1005Metric; Voltage 16V; Tolerance 10%
C4, C8, C11: 0.1uF; C_0603_1608Metric; Voltage 100V; Tolerance 10%
C5: 10nF; C_0402_1005Metric; Voltage 100V; Tolerance 10%
C6, C7, C9, C10: EEE-TK1J221AQ; CAP_PAN_EEE_H13_PAN
C12, C13, C14, C15, C16, C17, C23, C24, C25, C26, C27, C28: 10nF; C_0402_1005Metric; Voltage 50V; Tolerance 10%
C34, C35: 1.0nF; C_0402_1005Metric; Voltage 50V; Tolerance 10%
D1: Red; LED_0603_1608Metric_Red
D2: Green; LED_0603_1608Metric_Green
H1, H2, H3, H4: MountingHole; MountingHole_3.2mm_M3
J1: Conn_01x10; PinHeader_1x10_P2.54mm_Vertical
J2: Conn_01x09; PinHeader_1x09_P2.54mm_Vertical
J3, J4: MKDS5_2-9_5_1pos_PowerPad
J5: MKDS5_2-9_5_4pos_PowerPad
J6, J7: Conn_01x04; PinHeader_1x04_P2.54mm_Vertical
JP1, JP2, JP3, JP4, JP5, JP6: Jumper_2_Bridged; Jumper_2_NO
NT1, NT2, NT3, NT4, NT5, NT6: NetTie_2; NetTie-2_SMD_Pad0.25mm
NT7: NetTie_2; NetTie-2_SMD_Pad2.0mm
NT8, NT9: NetTie_2; NetTie-2_SMD_Pad0.5mm
Q1, Q2, Q3, Q4, Q5, Q6, Q7, Q8: CSD18540Q5B; TRANS_CSD18540Q5B; PARTREV B
R1, R3: 200; R_0402_1005Metric
R2, R12, R13, R14, R15, R16, R24, R25, R26, R27, R28: 10k; R_0402_1005Metric
R4, R9: PA2512FKE7T0U5E; RES_PA2512_YAG
R6: 100k; R_0402_1005Metric
R7: 330; R_0402_1005Metric
R8: 3.3k; R_0402_1005Metric
R10, R22: 20k; R_0402_1005Metric
R11, R23: 0; R_0402_1005Metric
R17, R18, R19, R20, R21, R29, R30, R31, R32, R33: 22; R_0402_1005Metric
SW1: SMD_5.2x5.2mm_h1.9mm; Push_SMD_4.6x2.8mm_h1.9mm
U1: DRV8704DCPR; DCP0038A_N
U2, U3: ADS1220xPW; TSSOP-16_4.4x5mm_P0.65mm

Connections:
+3.3V: C21.2, C22.1, C32.2, C33.1, J1.1, J2.1, R1.2, R2.1, R8.1, SW1.1, U2.12 (AVDD), U2.13 (DVDD), U3.12 (AVDD), U3.13 (DVDD)
+5V: C1.2, R3.1, U1.6 (V5)
/A1HS: Q1.4, U1.36 (A1HS)
/A1LS: Q2.4, U1.35 (A1LS)
/A2HS: Q3.4, U1.31 (A2HS)
/A2LS: Q4.4, U1.32 (A2LS)
/AIN1: J2.6, U1.10 (AIN1)
/AIN2: J2.7, U1.11 (AIN2)
/AISENP: C34.2, Q2.1, Q2.2, Q2.3, Q4.1, Q4.2, Q4.3, R4.2, U1.34 (AISENP)
/AOUT1: NT1.1, U1.37 (AOUT1)
/AOUT2: NT2.2, U1.30 (AOUT2)
/B1HS: Q5.4, U1.27 (B1HS)
/B1LS: Q6.4, U1.26 (B1LS)
/B2HS: Q7.4, U1.22 (B2HS)
/B2LS: Q8.4, U1.23 (B2LS)
/BIN1: J2.8, U1.12 (BIN1)
/BIN2: J2.9, U1.13 (BIN2)
/BISENP: C35.2, Q6.1, Q6.2, Q6.3, Q8.1, Q8.2, Q8.3, R9.2, U1.25 (BISENP)
/BOUT1: NT3.1, U1.28 (BOUT1)
/BOUT2: NT4.2, U1.21 (BOUT2)
/CS_T1: J1.7, R20.2
/CS_T2: J1.8, R32.2
/DRDY_N_T1: J1.9, R21.2
/DRDY_N_T2: J1.10, R33.2
/FAULT_N: D1.1 (K), J2.5, R2.2, U1.18 (FAULT_N)
/MA1: J5.4, NT1.2, Q1.1, Q1.2, Q1.3, Q2.5_6_7_8
/MA2: J5.3, NT2.1, Q3.1, Q3.2, Q3.3, Q4.5_6_7_8
/MB1: J5.2, NT3.2, Q5.1, Q5.2, Q5.3, Q6.5_6_7_8
/MB2: J5.1, NT4.1, Q7.1, Q7.2, Q7.3, Q8.5_6_7_8
/R0N_T1: J6.3, JP1.2 (B), NT5.2, R14.1
/R0N_T2: J7.3, JP4.2 (B), NT6.2, R26.1
/R0P_T1: J6.4, JP1.1 (A), R10.2, R12.1, R13.1
/R0P_T2: J7.4, JP4.1 (A), R22.2, R24.1, R25.1
/R1N_T1: J6.1, JP2.2 (B), JP3.1 (A), R16.1
/R1N_T2: J7.1, JP5.2 (B), JP6.1 (A), R28.1
/R1P_T1: J6.2, JP2.1 (A), NT5.1, R15.1
/R1P_T2: J7.2, JP5.1 (A), NT6.1, R27.1
/RESET: J2.4, SW1.2, U1.9 (RESET)
/RSVD: U1.20 (RSVD)
/SCLK: J1.3, R17.2, R29.2, U1.14 (SCLK)
/SCS: J1.6, U1.16 (SCS)
/SDI: J1.4, R18.2, R30.2, U1.15 (SDATI)
/SDO: J1.5, R8.2, R19.2, R31.2, U1.17 (SDATO)
/SLEEP_N: R6.2, R7.1, U1.8 (SLEEP_N)
/SLEEP_N_IN: J2.3, R7.2
GND: C1.1, C3.1, C5.1, C6.2, C7.2, C8.2, C9.2, C10.2, C11.2, C34.1, C35.1, D2.1 (K), J4.1, NT8.1, NT9.2, R4.1, R6.1, R9.1, U1.5 (GND), U1.19 (GND), U1.24 (BISENN), U1.29 (GND), U1.33 (AISENN), U1.38 (GND), U1.39 (PAD)
GNDA: C12.1, C13.1, C14.1, C15.1, C16.1, C17.1, C22.2, C23.1, C24.1, C25.1, C26.1, C27.1, C28.1, C33.2, JP3.2 (B), JP6.2 (B), NT7.2, U2.5 (AVSS), U3.5 (AVSS)
GNDD: C21.1, C32.1, J1.2, J2.2, NT7.1, NT8.2, NT9.1, U2.3 (CLK), U2.4 (DGND), U3.3 (CLK), U3.4 (DGND)
unnamed: D1.2 (A), R1.1
unnamed: D2.2 (A), R3.2
unnamed: R10.1, R11.1
unnamed: R22.1, R23.1
unnamed: C4.1, U1.1 (CP1)
unnamed: C4.2, U1.2 (CP2)
unnamed: C2.1, U1.3 (VCP)
unnamed: C3.2, U1.7 (VINT)
unnamed: C14.2, C18.1, R13.2, U2.11 (AIN0/REFP1)
unnamed: C15.2, C18.2, R14.2, U2.10 (AIN1)
unnamed: C16.2, C19.1, R15.2, U2.7 (AIN2)
unnamed: C17.2, C19.2, R16.2, U2.6 (AIN3/REFN1)
unnamed: R18.1, U2.16 (DIN)
unnamed: R19.1, U2.15 (DOUT/~DRDY)
unnamed: C13.2, C20.2, R12.2, U2.8 (REFN0)
unnamed: C12.2, C20.1, R11.2, U2.9 (REFP0)
unnamed: R17.1, U2.1 (SCLK)
unnamed: R20.1, U2.2 (~CS)
unnamed: R21.1, U2.14 (~DRDY)
unnamed: C25.2, C29.1, R25.2, U3.11 (AIN0/REFP1)
unnamed: C26.2, C29.2, R26.2, U3.10 (AIN1)
unnamed: C27.2, C30.1, R27.2, U3.7 (AIN2)
unnamed: C28.2, C30.2, R28.2, U3.6 (AIN3/REFN1)
unnamed: R30.1, U3.16 (DIN)
unnamed: R31.1, U3.15 (DOUT/~DRDY)
unnamed: C24.2, C31.2, R24.2, U3.8 (REFN0)
unnamed: C23.2, C31.1, R23.2, U3.9 (REFP0)
unnamed: R29.1, U3.1 (SCLK)
unnamed: R32.1, U3.2 (~CS)
unnamed: R33.1, U3.14 (~DRDY)
VBUS: C2.2, C5.2, C6.1, C7.1, C8.1, C9.1, C10.1, C11.1, J3.1, Q1.5_6_7_8, Q3.5_6_7_8, Q5.5_6_7_8, Q7.5_6_7_8, U1.4 (VM)

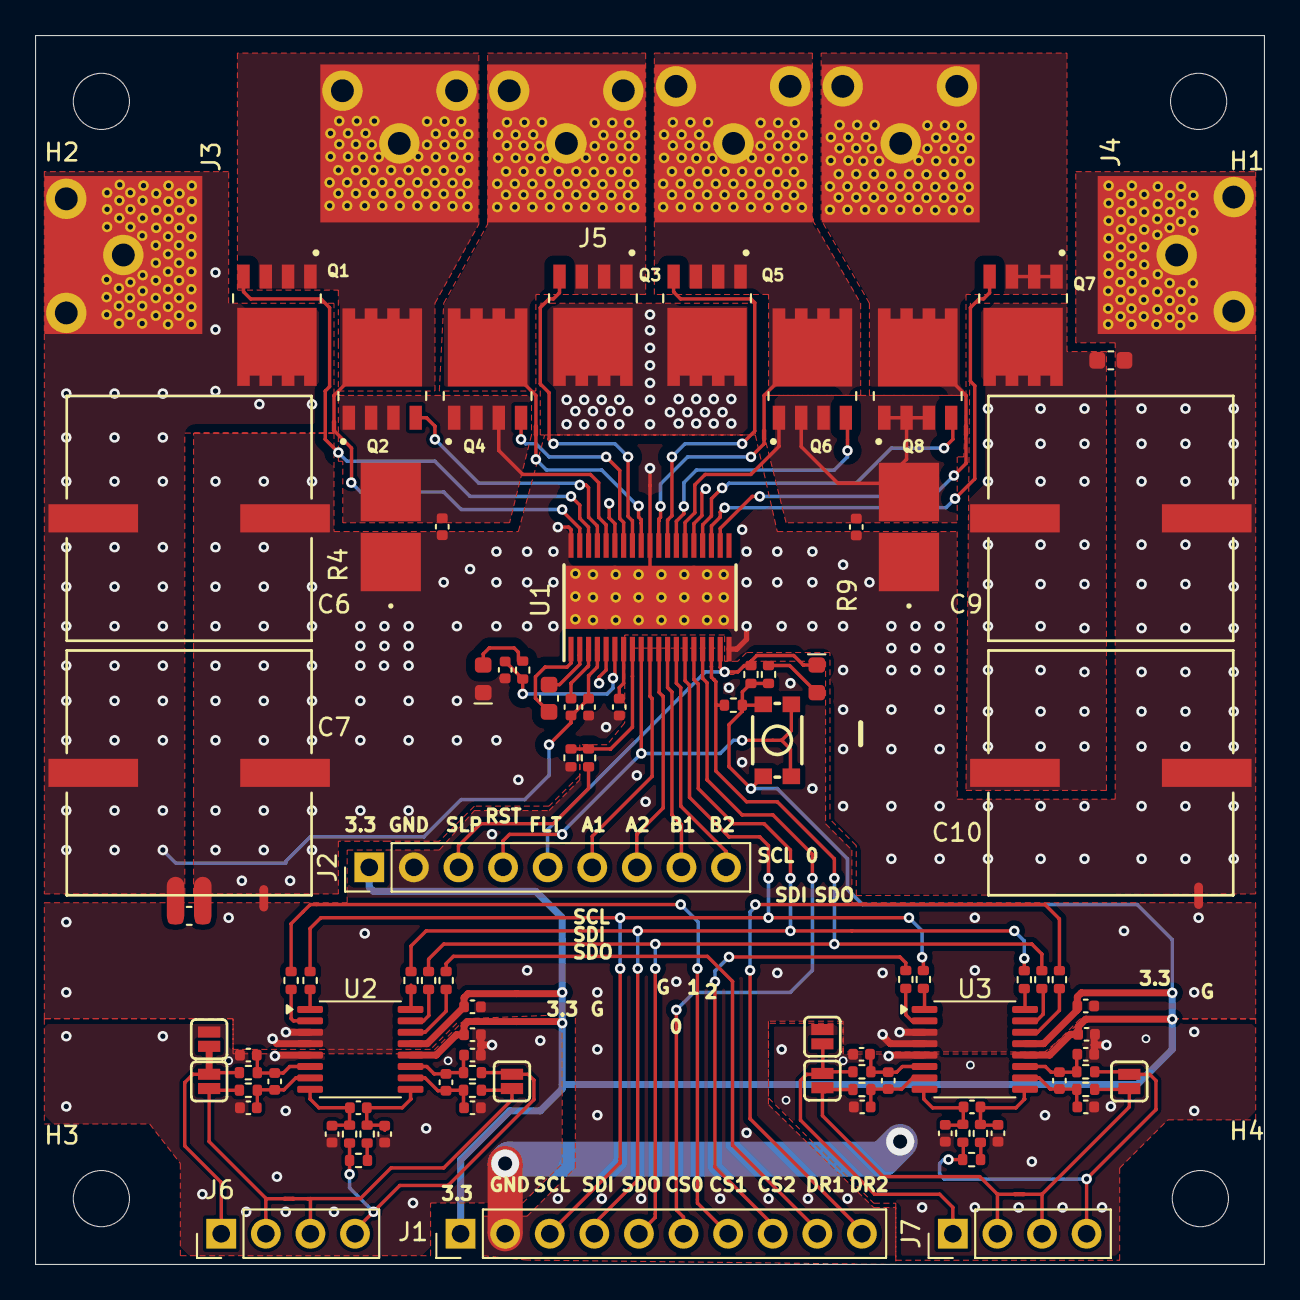
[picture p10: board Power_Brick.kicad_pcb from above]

Board: 2 copper layers, 70.0 x 70.0 mm, 107 parts (0 on the bottom side), 78 nets.

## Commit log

2025-12-11 TI options
    [DRV8701EVM.GBL, DRV8701EVM.GBO, DRV8701EVM.GBP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]
2025-12-12 KiCad beta
    [Power_Brick.kicad_pcb, Power_Brick.kicad_sch]
2025-12-16 Beta Design
    [DRV8701EVM.GBL, DRV8701EVM.GBO, DRV8701EVM.GBP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]
2026-01-28 Revised fault and capacitor ratings
    [Power_Brick.kicad_pcb, Power_Brick.kicad_sch]
2026-01-28 DRC, Silkscreen Updates
    [Power_Brick.kicad_pcb]
2026-02-03 Digital Grount Updates
    [DC Power Brick BOM.xlsx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]
2026-02-08 4 oz copper 0.3mm clearance
    [Power_Brick-B_Cu.gbr, Power_Brick-B_Mask.gbr, Power_Brick-B_Paste.gbr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]
